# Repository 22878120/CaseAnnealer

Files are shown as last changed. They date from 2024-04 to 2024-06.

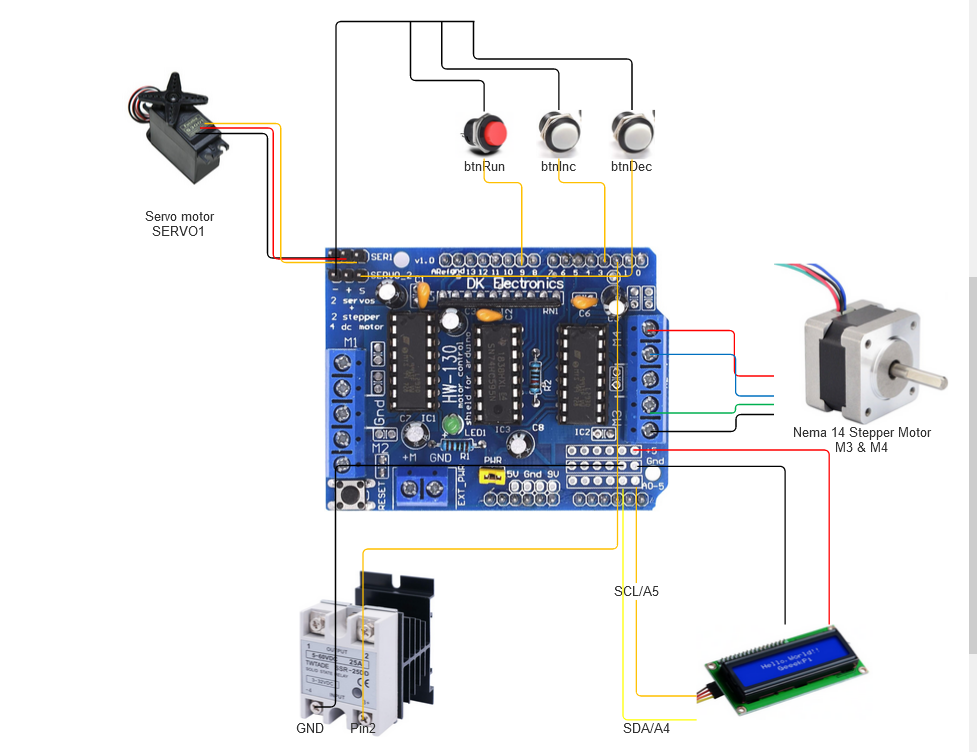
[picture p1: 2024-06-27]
CIrcuit diagrams/CaseAnnealer - MotorShield Circuit diagram.png

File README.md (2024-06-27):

# CaseAnnealer

Rifle cases induction annealing project. Never anneal pistol cases as it can soften the base resulting in catastrophic failure.  
The 3D prints for the feeder I got it from [Thingiverse](https://www.thingiverse.com/thing:4902058), but the case dropper files are attached as STL for printing.

Please note that I used old uno and shield boards just because it was laying around, you can modify them as you want if you prefer to use different components

# Components & cost breakdown...

| Item | Aprox cost |
| --- | --- |
| [Power supply](https://www.amazon.com/gp/product/B0CSZ3W983/ref=ppx_yo_dt_b_search_asin_title?ie=UTF8&psc=1) | $40.00 |
| [1000W Low Voltage Induction Heating Board:](https://www.amazon.com/gp/product/B01C70G7Y8/ref=ppx_yo_dt_b_search_asin_title?ie=UTF8&psc=1) | $46.80 |
| [Adhesive Cable Clips](https://www.amazon.com/gp/product/B0BV3CSZ5V/ref=ppx_yo_dt_b_search_asin_title?ie=UTF8&th=1) | $3.20 |
| [Brass Compression Tube Fitting](https://www.amazon.com/gp/product/B075L98VNH/ref=ppx_yo_dt_b_search_asin_title?ie=UTF8&psc=1) | $7.60 |
| [Copper Tubing 1/4" OD × 3/16" ID × 3FT](https://www.amazon.com/gp/product/B0BLNRX31W/ref=ppx_yo_dt_b_search_asin_title?ie=UTF8&psc=1) | $8.50 |
| [Insulation Braid Sleeving](https://www.amazon.com/gp/product/B082YJFZVQ/ref=ppx_yo_dt_b_search_asin_title?ie=UTF8&psc=1) | $9.11 |
| [DROK DC-DC Buck Volt Converter, DC 20-90V to 12V 6A](https://www.amazon.com/gp/product/B0C4L77WMP/ref=ppx_yo_dt_b_search_asin_title?ie=UTF8&psc=1) | $18.00 |
| [SSR-25 DD 10A DC 3-32V to DC 5-60V SSR Solid State Relay + Heat Sink](https://www.amazon.com/gp/product/B079BBZL7F/ref=ppx_yo_dt_b_search_asin_title?ie=UTF8&psc=1) | $10.60 |
| [16MM Momentary Push Button ON Off Switch Assorted](https://www.amazon.com/gp/product/B08SKJ6V7Z/ref=ppx_yo_dt_b_search_asin_title?ie=UTF8&psc=1) | $12.18 |
| [PVC Hose Tube, 8mm](https://www.amazon.com/gp/product/B08GJXDLM9/ref=ppx_yo_dt_b_search_asin_title?ie=UTF8&psc=1) | $5.50 |
| [ZVS 12V Water Cooling Pump](https://www.amazon.com/gp/product/B00MB9EP3G/ref=ppx_yo_dt_b_search_asin_title?ie=UTF8&psc=1) | $22.93 |
| [Arduino Uno REV3](https://www.amazon.com/Arduino-A000066-ARDUINO-UNO-R3/dp/B008GRTSV6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) | $27.60 |
| [L293D DC Motor Drive Shield Stepper Motor](https://www.amazon.com/gp/product/B08J1N7DCN/ref=ppx_yo_dt_b_search_asin_title?ie=UTF8&psc=1) | $7.50 |
| [Nema 14 Stepper Motor](https://www.amazon.com/gp/product/B00PNEPZQC/ref=ppx_yo_dt_b_search_asin_title?ie=UTF8&psc=1) | $21.00 |
| [Servo motor](https://www.amazon.com/Standard-Futaba-Tamiya-Kyosho-Duratrax/dp/B09TQ245VH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) | $10.00 |
| [I2C 1602 LCD Display Module 16X2](https://www.amazon.com/gp/product/B07S7PJYM6/ref=ppx_yo_dt_b_search_asin_title?ie=UTF8&psc=1) | $11.00 |

Aprox total cost $261.52

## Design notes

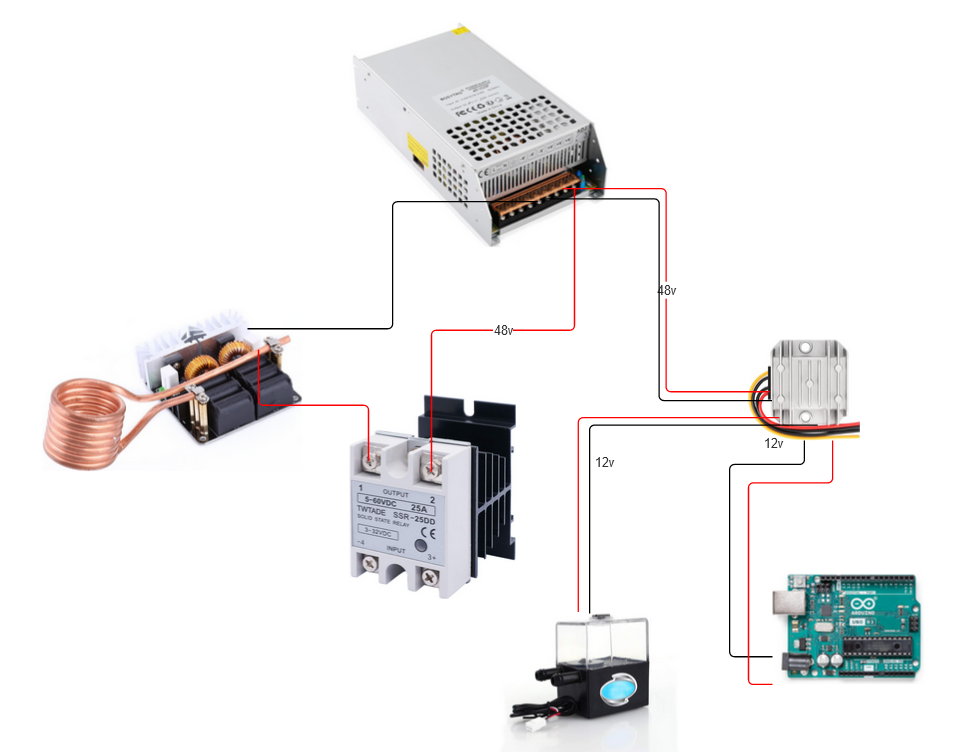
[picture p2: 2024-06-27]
CIrcuit diagrams/CaseAnnealer - Power Circuit diagram.png

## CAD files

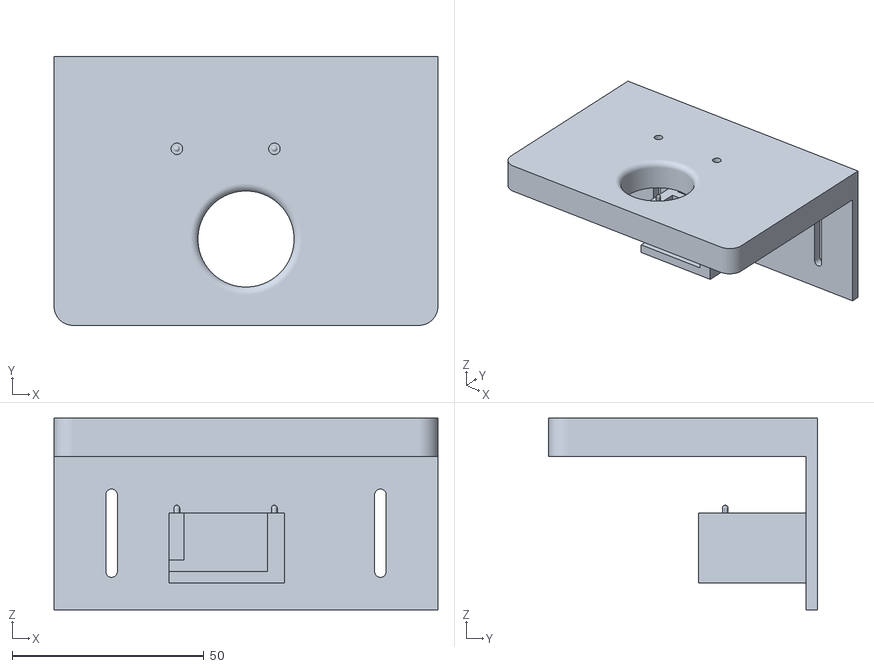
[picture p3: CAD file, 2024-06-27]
3D print/Case dropper - Body.stl
100.0 x 70.0 x 50.0

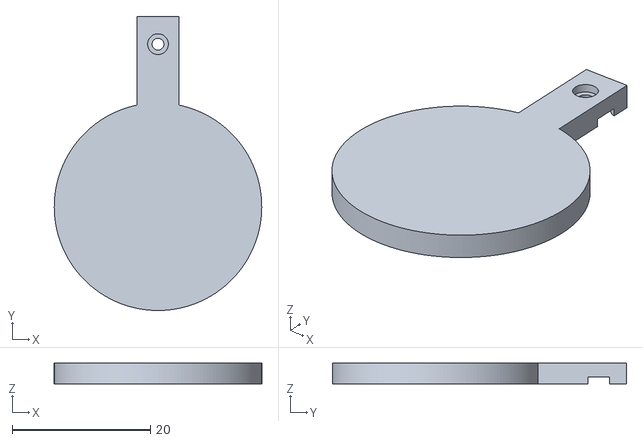
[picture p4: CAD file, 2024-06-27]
3D print/Case dropper - Lip.stl
30.0 x 42.5 x 3.00

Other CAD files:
3D print/Annealer - Case Dropper v9.f3z

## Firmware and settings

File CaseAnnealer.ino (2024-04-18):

#include <AFMotor.h>
#include <Servo.h>
#include <EEPROM.h>

// LCD I2C 1602 LCD Display Module 16X2
#include <Wire.h>
#include <LiquidCrystal_I2C.h>

// DC hobby servo
// Servo1 (signal) >> Pin10
// Servo2 (Signal) >> Pin9
// motor range 20-165
Servo servo1;


#include <ezButton.h>
ezButton btnRun(9);       // servo2 not used
ezButton btnInc(3);       // M2 not used
ezButton btnDec(11);      // M1 not used



//Global var for anneal duration
float annealing_duration = 3.00;  //time in sec, default 3 sec
const String sAnnealingReady = "Annealing ready";
const String sAnnealingRun = "Annealing run";
const String sChangeTiming = "Red btn to save";
bool isIdle = true;
bool isChangeTime = false;
bool isRequestCancel = false;



// Relay
int relayPin = 2;  //Pin 2

//Specifics for my servo
int servo_min = 25;
int servo_max = 160;
int servo_mid = 93; // the servoe start pos

// Stepper motor on M3+M4 200 steps per revolution
// M1 -> Pin 11
// M2 -> Pin 3
AF_Stepper stepper(200, 2);


// LCD
LiquidCrystal_I2C lcd(0x27, 16, 2); // set the LCD address to 0x27, if new version please use 0x3F instead.


// --------------------------------------------------------------------------------------------------------------
void showLCD(String msgLn1="", String msgLn2="", int lcd_delay=500 ) { 
  // Fill text with space to clear screen
  for (int i = msgLn1.length(); i <=16; i++) {
    msgLn1 = msgLn1 + " ";
  }

  for (int i = msgLn2.length(); i <=16; i++) {
    msgLn2 = msgLn2 + " ";
  }

  lcd.setCursor(0, 0); // set the cursor to column 0, line 0
  lcd.print(msgLn1);  // Print a message to the LCD
  
  lcd.setCursor(0, 1); // set the cursor to column 0, line 1
  lcd.print(msgLn2);  // Print a message to the LCD.

  // Serial.println(msgLn1);
  // Serial.println(msgLn2);

  delay(lcd_delay);  
}

void DoAnnealing () {
  unsigned long StartTime;
  unsigned long EndTime;
  char str[5];  // Allocate a character array to store the resul
  const String sStartAnn = "Annealing";
  String sCancelRequested = "";

  showLCD(sStartAnn);
  Serial.println(sStartAnn);


  StartTime = millis();

  digitalWrite(relayPin,HIGH);  	// turn the relay ON
								// [NO] is connected to feed
								// [NC] is not connected to feed

  while ((millis()-StartTime) < (annealing_duration*1000)) {
    CheckRunPressDuringExecution();
    if (isRequestCancel) {
      sCancelRequested = " - CR";
    } 

    dtostrf((millis()-StartTime)/1000.00, 4, 2, str);
    showLCD(sStartAnn+sCancelRequested, String(str) + " sec", 0);
  }  				

  EndTime = millis();
	digitalWrite(relayPin,LOW);  	// turn the relay OFF
								// [NO] is not connected to feed
								// [NC] is connected to feed

  showLCD("Annealing finished", "Time: "+String((EndTime - StartTime)/1000)+" sec", 1000);
  Serial.println("Annealing finished / Time: "+String((EndTime - StartTime)/1000)+" sec");
}

void CaseFeed() {
  const String sCaseFeed = "Feed case";
  showLCD(sCaseFeed);
  Serial.println(sCaseFeed);

  stepper.setSpeed(50);

  // stepper.step(400, FORWARD, INTERLEAVE); //too fast
  stepper.step(200, FORWARD, MICROSTEP);
  // stepper.step(200, FORWARD, DOUBLE);

  stepper.release(); // stop rotation and turn off holding torque.
}

void CaseRelease() {
  const String sReleaseCase = "Release case";
  showLCD(sReleaseCase);
  Serial.println(sReleaseCase);

  servo1.write(servo_min);
  delay(500);  //1000 ms = 1 sec
  servo1.write(servo_mid);
}

String GetAnnealTime() {
  return "Time: "+String(annealing_duration)+" sec";
}

void AnnealOneCycle() {
  CaseFeed();
  CheckRunPressDuringExecution();

  DoAnnealing();
  CheckRunPressDuringExecution();

  CaseRelease();

  unsigned long StartTime;
  unsigned long TotalWaitTime = 0;

  StartTime = millis();

  while (TotalWaitTime < 2000) {
    CheckRunPressDuringExecution();
    TotalWaitTime = millis() - StartTime;
  }
}

void CheckRunPressDuringExecution() {
  btnRun.loop();
  if (btnRun.isPressed()) {
    const String sCancelReq = "Cancel requested";
    isRequestCancel = true;
    showLCD(sCancelReq, "");
    Serial.println(sCancelReq);
    // delay(1000);
  }
}

void setup() {

  //--------------------------------------------------------------------------------------------------------------------
  // LCD
  lcd.init();  //initialize the lcd
  lcd.backlight();  //open the backlight
  showLCD("LCD ready");

  //--------------------------------------------------------------------------------------------------------------------
  Serial.begin(9600);           // set up Serial library at 9600 bps

  //--------------------------------------------------------------------------------------------------------------------
  // Relay setup
  pinMode(relayPin, OUTPUT);  	// Define the port attribute as output   
  digitalWrite(relayPin, LOW);    // switch off relay:  
  showLCD("Relay ready");

  //--------------------------------------------------------------------------------------------------------------------
  // turn on servo
  servo1.attach(10);

  if (servo1.read() == servo_mid) {
    showLCD("Case door closed.", 
            "Pos: "+String(servo1.read())+", "+servo1.readMicroseconds()+" ms");
  }


  //--------------------------------------------------------------------------------------------------------------------
  // turn on stepper motor #2
  stepper.setSpeed(200);
  showLCD("Feeder motor", "ready...");


  // Get stored anneal time
  EEPROM.get(0, annealing_duration);
  showLCD(sAnnealingReady, GetAnnealTime());
}

void loop() {
  
  btnInc.loop();
  btnDec.loop();
  btnRun.loop();

  if (btnRun.isPressed() || isRequestCancel) {
    if (isIdle){  //Idle & change -> Save value
      if (isChangeTime) { //Save
        EEPROM.put(0, annealing_duration);
        isChangeTime = false;
        
        showLCD("Timing saved", GetAnnealTime());
        delay(1000);
        showLCD(sAnnealingReady, GetAnnealTime());
      } else {  //Idle & no change -> RUN
        isIdle = false;
        showLCD(sAnnealingRun, ""); //will run after exit this IF
      }
    } else {  // not idel (running) -> Cancel run
      isIdle = true;
      isRequestCancel = false;
      showLCD("Canceling...", GetAnnealTime());
      delay(1000);
      showLCD(sAnnealingReady, GetAnnealTime());
    }
  }

  //If running, keep running
  if (!isIdle) {
    AnnealOneCycle();
  }

  // Inc/Dec buttons can be used only in Idel
  if (isIdle) {
    if (btnInc.isPressed()){
      annealing_duration = annealing_duration + 0.1;
      isChangeTime = true;
      showLCD(sChangeTiming, GetAnnealTime(), 0);
    }

    if (btnDec.isPressed()){
      annealing_duration = annealing_duration -0.1;
      if (annealing_duration < 0) {
        annealing_duration = 0;
      }
      isChangeTime = true;
      showLCD(sChangeTiming, GetAnnealTime(), 0);
    }
  }

  delay(100);
}

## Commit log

2024-04-18 add timer count LCD view
2024-06-27 Add circuit diagrams and 3D designs
2024-06-27 update the project
    [Annealer - Case Dropper v9.f3z, Case dropper - Body.stl, Case dropper - Lip.stl]
2024-06-27 Update files
    [Annealer - Case Dropper v9.f3z, Case dropper - Body.stl, Case dropper - Lip.stl]
